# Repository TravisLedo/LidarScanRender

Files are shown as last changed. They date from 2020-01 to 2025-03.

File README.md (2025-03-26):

# Lidar Scan & Render Bot

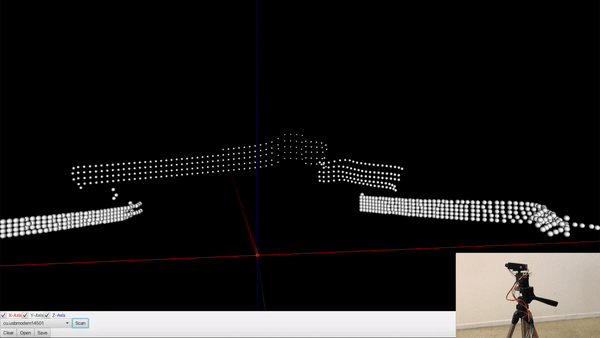
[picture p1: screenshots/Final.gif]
Results


## Video Link

* [YouTube](https://youtu.be/6YTCKRSWroE) - Video Demo

## How It Works
This project consists of two parts. The Arduino side handles all the servo movements and gets measurement readings from the Lidar sensor. The Java side does the spherical to cartesian points conversion and renders them in 3D. They communicate with each other over the serial port. The user can move around the scene with game-like fps controls for a better experience.

## The Math
There are two servos in the project. One will be used as the Pan (Phi) angle and the other as the Tilt (Theta) angle. The reading we get from the Lidar sensor will become the Radius. Which means that device itself would be at point (0,0,0). Each data set sent from the Arduino to the Java program consists of these three numbers (radius, phi, theta) with leading zeroes for consistency.

From here we have to convert these Spherical points to Cartesian(x, y, z) so we can properly plot them in our Java program.

We can achieve these conversions using these formulas.

Note: If you look inside the Java code and notice that some of the values of x, y, and z are swapped, some times even set to negative, that's because the computer coordinate system is different as well. For example, in computer coordinates, the x goes horizontal not y. Y positive goes down, not up. Things like that. These modifications made to the formula were only to get Java to render the points in the correct place.

## Serial Communication
I started this project with an Arduino Uno but ran into problems with the serial port conflicting with the servos. They cannot work at the same time. When data was being sent back and forth, the servos would jitter constantly. From research I learned that this was a common problem using SoftwareSerial. I found some workarounds for this problem but they were such a hassle and didn't work for me. I decided to switch to an Arduino Mega and it solved the jittering problem. This is because the Mega has multiple serial ports.

The steps of communicating

-Java opens port and listens for data
-Arduino takes first measurement, moves the servos to the next position and wait for an "Okay" signal from Java
 Arduino sends the data to Java in this format 000,000,000
-Java waits for all the fragments of data to reach a certain amount that is enough to convert
-Java converts those numbers, plots the point, and send the Arduino a single char as the "Okay" signal
-Once the Arduino receives the signal, it repeats what it did before at the new angle positions

The reason Java has to wait is because even though you tell the Arduino to send 9 digits and 2 commas, sending data over serial does not work that way. It will send fragments of whatever data it wants whenever it can. So we want Java to until all the data received looks like something it can recognize.

I used a USB cable as the serial connection but I am sure one could use a bluetooth module as well if wireless was needed.

## Powering The Project
I used a 5v wall brick to run the servos because I just hate dealing with batteries and avoid them when possible. The Lidar sensor was powered through the Arduino 5V. And of course the Arduino was powered with the same USB cable that was used as a serial port.

### Materials
* [Arduino Mega 2560](https://amzn.to/4c5rFt3)
* [Lidar Sensor](https://amzn.to/3XwOXC2)
* [Servo Motors](https://amzn.to/42jcc5k)
* [Brackets](https://amzn.to/3FSMJGZ)

### Prerequisites

* [Java](https://www.java.com) - Java Runtime Environment
* [Arduino](https://www.arduino.cc/) - Arduino Mega Microcontroller
* [TFMini(UART)](https://www.sparkfun.com/products/14588) - TFMini Lidar sensor

* [MG996R Servo x 2](https://www.towerpro.com.tw/product/mg996r/) - 180 degrees standard servos

## Programmed In

* [IntelliJ](https://www.jetbrains.com/idea/download) - Java IDE
* [Arduino](https://https://www.arduino.cc/) - Arduino IDE

## Schematic

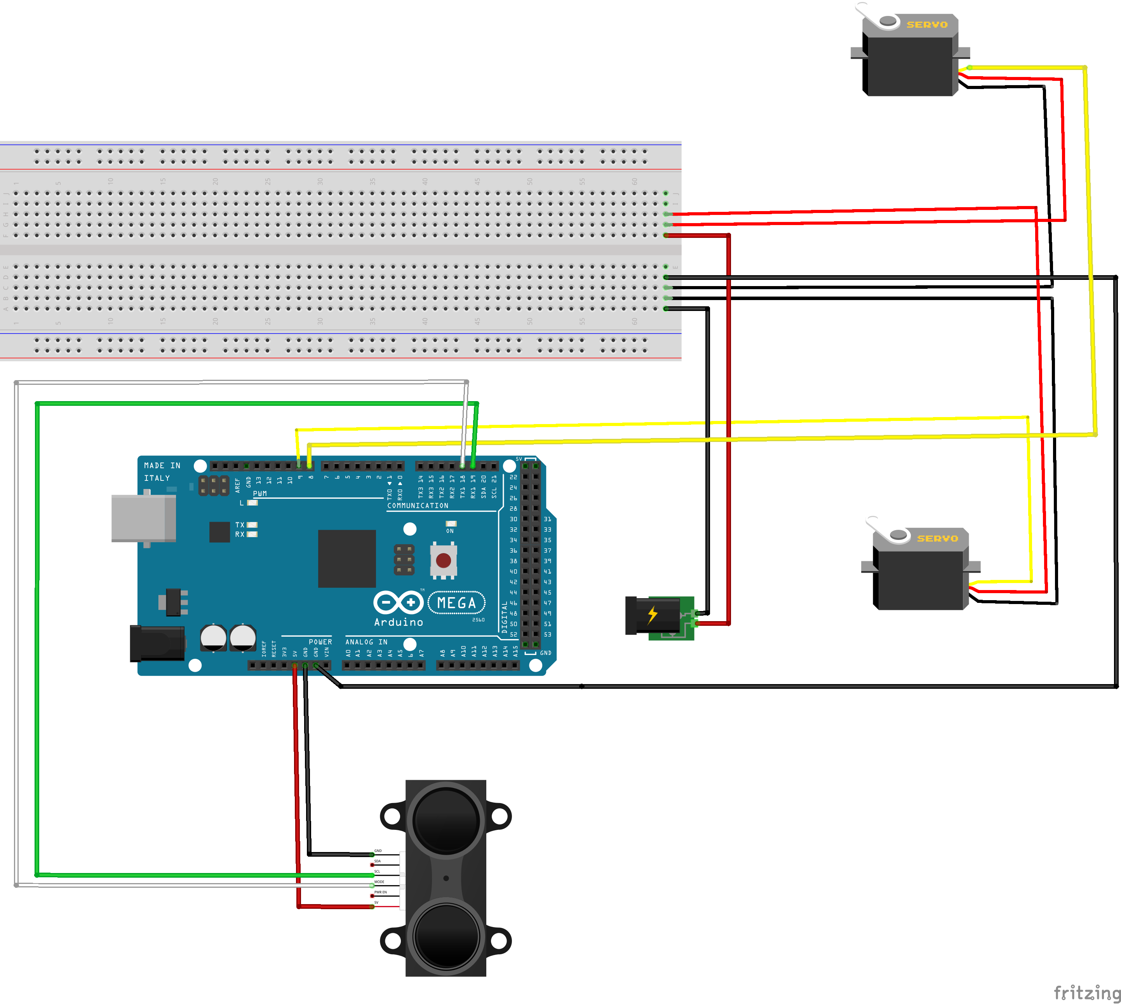
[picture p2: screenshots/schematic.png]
Schematic


## Screenshots

The Device
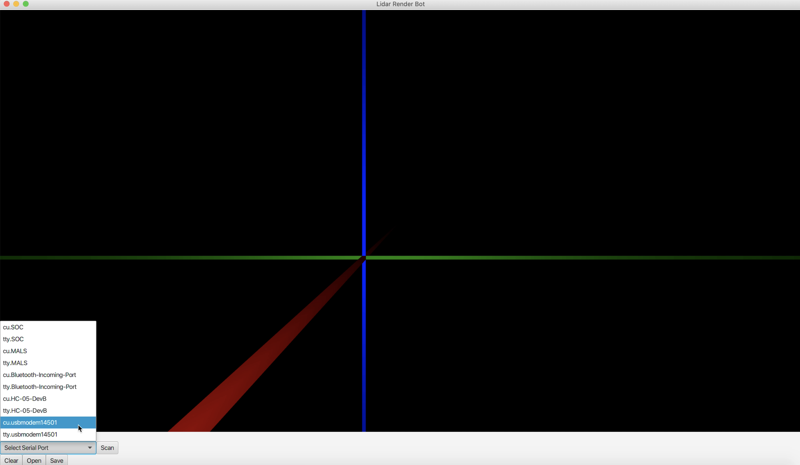
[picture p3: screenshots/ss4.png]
The Software

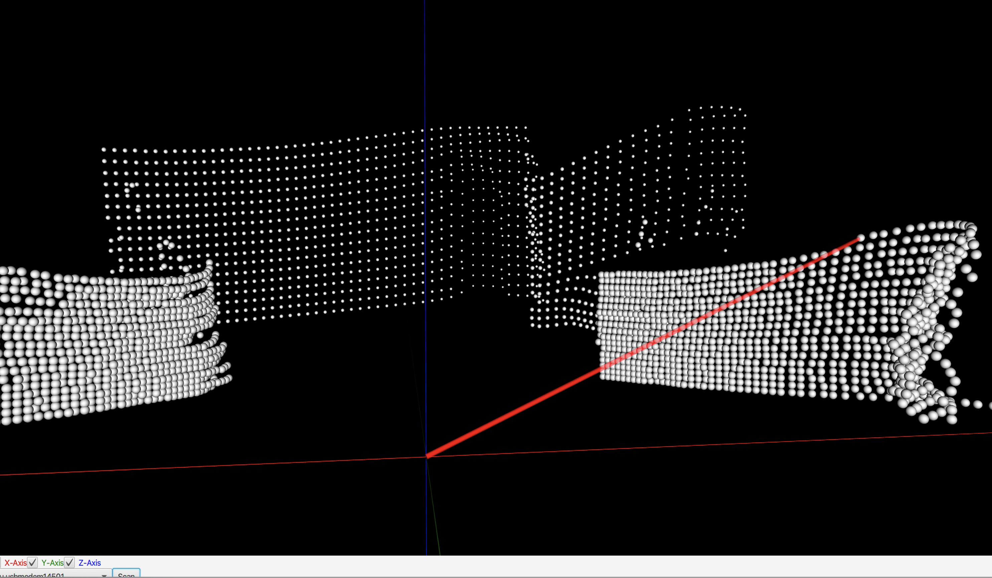
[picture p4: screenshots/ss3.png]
Running The Program

Results

## Authors

* **[Travis Ledo](https://travisledo.github.io)** - *Initial work* - [LidarScanRender](https://github.com/TravisLedo)

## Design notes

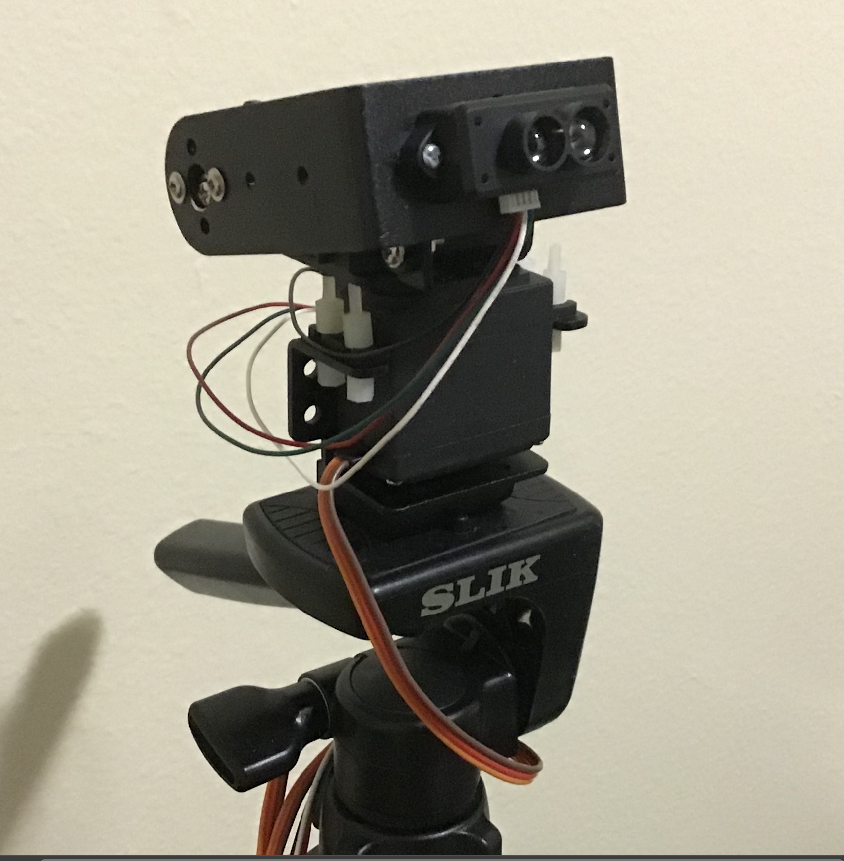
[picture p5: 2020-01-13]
screenshots/ss1.png

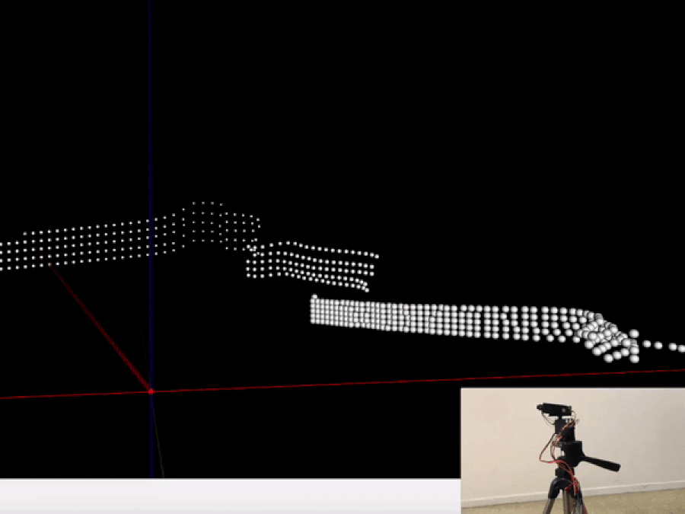
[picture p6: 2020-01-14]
screenshots/FinalCroppedGif.gif

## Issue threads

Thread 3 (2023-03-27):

Data not outputting correctly

tpats98, 2023-03-27:
Hi Travis,

I am a graduate student working on a project to eventually be able to scan and map underwater interiors such as caves and wrecks. I found your project and have been attempting to replicate it in my own way. I'm using Arduino to control my servo/LiDAR system as well as perform the conversion calculations. The sensor I am using is a Garmin LiDAR Lite v3HP. I use Putty to put the data into an Excel file and I am then using a Matlab code to put that data into a point cloud format. So, it is not happening live as in your scan. I am running into issues where the point cloud that is created looks nothing like the room I scanned. One of the issues is I am not getting any straight edges as if it was scanning a wall. It seems as though it is giving me a circle just based on the cloud I am seeing. The point clouds just do not make sense compared to what it should be scanning. I attempted to attach a screenshot, I am not sure if it is visible. Overall, it seems that my inputs are good. I am getting my pan and tilt servo positions as well as a distance reading from my sensor. This makes me think the issue is somewhere in my calculations and post-processing or maybe it could be an issue with my sensor/setup itself.

I am new to Github so I wasn't sure how to reach you. My apologies if this isn't the appropriate way to contact you. I was hoping you might be willing to provide some aid to me as I try to solve my issues. I look forward to hearing from you!

Thank you,
Tim Patschorke

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

TravisLedo, 2023-03-27:
Hey Tim,

Thanks for taking interest in this project and your app is looking really good.

When making your points render on screen, did you account for all the conversions? You have to convert from spherical coordinates, to rectangular coordinates, and then also to computer screen coordinates as well. Screens have minor differences like the Y axis going down for positive, not up. I would start a simple scan with just a few points first where you kind of know what the results should be and then play around with the conversions until it looks right. Even better if you test with just only one servo at a time to eliminate one axis from the conversions.

Another thing to make sure is that you are not using an Arduino UNO, the MEGA is a better choice. This project requires more than one serial line. One for sending data to pc and also another for getting data from the lidar sensor to the Arduino.  They interfere with each other if there is only one and the software serial libraries also will not work.

I am sure you have done this but have u also tried just testing the sensor itself? Just moving your hand back and forth to make sure the distance output looks correct.

Hope one of these could help you solve the problem. Let me know how it goes. Good luck!

tpats98, 2023-03-27:
Hi Travis,

Thank you for the timely response. I am mostly accounting for the conversions. I am having my Arduino code perform the spherical to cartesian as it scans. I have done a little bit of tinkering with the conversion for the computer coordinate system but not as much.

I tried taking out an axis, as you mention, by only using the pan servo. I played around with this and different things over the weekend and the only thing that would make my cloud look remotely close was by creating my own range for x. Instead of using the data, I just created a 0-180 range that the distance value could be plotted against. This gave me a somewhat accurate depiction of what was in front of the sensor but it is not a true representation of the room obviously.

As for the board, I am using a Mega. I haven't run into any issue whatsoever in the actual operation of the servos and sensor so that is a plus haha.

As for the sensor, you are correct, I have tested it by itself. I did not see any problems jumping out at me.

Overall, do you think my issue is just in the conversions possibly? I guess my main confusion is why it is outputting as a half circle instead of straight lines as if it was scanning a wall or came to a corner. Any ideas on that other than conversion issues maybe?

TravisLedo, 2023-03-27:
Yea I am leaning towards a conversion issue, especially when it looks more spherical when plotted. I would try to send manual data from the Arduino into the app as well to see if you get what you expect on the screen. Start with with something simple like (0,0,0, (10,10,10) and see if the two points are plotting correctly then add more points to the test.  If this looks good then most likely a conversion issue.

Have you tried dramatically slowing down the servos' delay between each point to give it more time to move to position, scan, move to the next position? Did you scan one point multiple times and play around with using the average or median? Try to get random readings and see how consistent the scanner is at one position.

Also have you tried a different wall? lol. I know that lidar sucks on glossy surfaces as well as sharp corners.

tpats98, 2023-03-29:
Hey Travis,

I wanted to reach out again as  I have good news! I spent the last 2 days messing around with the conversions and it is looking like I am getting the scan I need. I have attached one in case you're interested. I just wanted to thank you again for pointing me in the right direction!
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

TravisLedo, 2023-03-29:
That is awesome to hear! Glad you got it resolved. Hope everything goes well with your underwater scanner project, it's looking really cool.

Closed 2023-03-29.

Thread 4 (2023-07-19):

Errors occuring when run

24harter, 2023-07-19:
Here is the error message that I have every time I set it to run, however no error appears when I hit build/build and clean.
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

TravisLedo, 2023-07-19:
>

Hey there, it looks like you are missing JavaFX library. That library is pretty confusing and is constantly changing. I would make sure you install that library first, specifically for your IDE.

24harter, 2023-07-19:
This is the library I have installed with the jar files in it:
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
With this I get the error above. Am I missing something or a different kind of error, I'm new to java so sorry if this seems like a stupid question.
Also, thanks for responding to my issue quickly, I really appreciate it.

TravisLedo, 2023-07-19:
> This is the library I have installed with the jar files in it: 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 The IDE is the latest installment of Netbeans With this I get the error above. Am I missing something or a different kind of error, I'm new to java so sorry if this seems like a stupid question. Also, thanks for responding to my issue quickly, I really appreciate it.

Hey no worries. I just updated the project to use Gradle. This will auto download all the libraries you need. I also changed to using IntelliJ so please download that and run instead of Netbeans. Let me know how it goes.

24harter, 2023-07-20:
I've switched over to IntelliJ and transferred all the files, however I'm currently stuck on trying to run it since figure out what configuration I need.

TravisLedo, 2023-07-20:
> I've switched over to IntelliJ and transferred all the files, however I'm currently stuck on trying to run it since figure out what configuration I need.

Make sure you delete all the files you had and just download the whole project again. Then open the project folder from IntelliJ (Not the main LidarScanRender folder but the sub one inside). Once it finish loading, right click on the App file and select Run. Tell me what errors you get.

24harter, 2023-07-20:
I have successfully ran the app, but when I connect it to the com port and hit scan, it doesn't seem to be working. The arduino has the code on it, but seems inactive when I click scan. None of the servos are moving and nothing is appearing on the app or intellij.

24harter, 2023-07-20:
I have checked my lidar sensor and servos and both were fine. I believe the issue is that my lidar sensor is a tf luna instead of a tf mini-s, as it was mislabelled

TravisLedo, 2023-07-20:
> I have checked my lidar sensor and servos and both were fine. I believe the issue is that my lidar sensor is a tf luna instead of a tf mini-s, as it was mislabelled

Ah gotcha. Just need to refactor the Arduino code to use your specific sensor's library instead of the one I am using. It should still work, but that will be beyond what I can help you with since I don't own that sensor (I don't even have the one I used on this project anymore either).. Maybe play around with the current sensor you have and see if you can get it working. The fun part any project is making it work for your needs and learning along the way.

Closed 2024-04-03.

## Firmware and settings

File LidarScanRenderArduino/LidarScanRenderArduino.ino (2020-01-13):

/*
   Program: Lidar Render Bot
   By: Travis Ledo
   Date: Jan 12th 2020
   Notes: This uses an Arduino Mega with multiple serial ports to avoid the SoftwareSerial and Servo conflicts.
*/




#include <Servo.h>
#include "CustomTFMini.h" //Needed to modify somecode in the original TFMini library

Servo tiltServo;
Servo panServo;

TFMini tfmini;

String incomingByte; // for incoming serial data

int minPanPos = 0;
int maxPanPos = 180;
int minTiltPos = 0;
int maxTiltPos = 90;

int panPos = minPanPos;    // variable to store the servo position
int tiltPos = minTiltPos;    // variable to store the servo position


bool keepScanning = true;
bool panForward = true;


void printPoint(int pan, int tilt, int dis) { //Java software will read these printed texts

  Serial.print(addLeadingZeros(pan));
  Serial.print(pan);
  Serial.print(",");
  Serial.print(addLeadingZeros(tilt));
  Serial.print(tilt);
  Serial.print(",");
  Serial.print(addLeadingZeros(dis));
  Serial.print(dis);
  Serial.println();

}




String addLeadingZeros(int number) //Add leading zeros so every number sent will always be 3 digits long for consistency
{
  String leadingZeros = "";

  if (number < 10)
  {
    leadingZeros = "00";
  }
  else if (number >= 10 && number < 100)
  {
    leadingZeros = "0";
  }
  else
  {
    leadingZeros = "";

  }

  return leadingZeros;
}




void updatePos() //move servos to next position
{
  if (panPos == maxPanPos)
  {
    panPos = 0;
    tiltPos++;
    panServo.write(panPos);
    tiltServo.write(tiltPos);
    delay(1000);
    keepScanning = true;
  }
  else if (panPos < maxPanPos)
  {
    panPos ++;
    panServo.write(panPos);
    delay(15);

    keepScanning = true;
  }

  if (tiltPos > maxTiltPos)
  {
    keepScanning = false;
  }
}




void takeMeasurement(int panPos, int tiltPos) //get a reading from the TFMini
{

  uint16_t dist1 = tfmini.getDistance();

  while (dist1 < 0 || dist1 > 1500)
  {
    dist1 = tfmini.getDistance();
  }


  uint16_t dist2 = tfmini.getDistance();

  while (dist2 < 0 || dist2 > 1500)
  {
    dist2 = tfmini.getDistance();
  }

  uint16_t dist3 = tfmini.getDistance();

  while (dist3 < 0 || dist3 > 1500)
  {
    dist3 = tfmini.getDistance();
  }



  uint16_t dist = dist1 + dist2 + dist3;

  uint16_t distAv = dist / 3;



  // Display the measurement
  printPoint(panPos, tiltPos, distAv);
  updatePos();
}





void setup() {

  panServo.attach(8);  // attaches the servo on pin
  tiltServo.attach(9);  // attaches the servo on pin

  // Step 1: Initialize hardware serial port 
  Serial.begin(115200); //For usb/bt data?

  // Step 2: Initialize the data rate for TFMini
  Serial1.begin(TFMINI_BAUDRATE);

  // Step 3: Initialize the TF Mini sensor
  tfmini.begin(&Serial1);

  panServo.attach(8);  // attaches the servo on pin
  tiltServo.attach(9);  // attaches the servo on pin
  tiltServo.write(tiltPos);
  panServo.write(panPos);
  delay(2000);


  //start first measurement
  takeMeasurement(panPos, tiltPos);

}



void loop() {

  if (tiltPos > maxTiltPos) //end program succesfully
  {
    keepScanning = false;
  }

  // send data only when you receive data:
  if (Serial.available() > 0 && keepScanning) {
    keepScanning = false; //need this to make the loop not go so fast
    takeMeasurement(panPos, tiltPos);
  }
}

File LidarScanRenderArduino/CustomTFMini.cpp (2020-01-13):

/*
Arduino driver for Benewake TFMini time-of-flight distance sensor. 
by Peter Jansen (December 11/2017)
This code is open source software in the public domain.

THIS SOFTWARE IS PROVIDED ''AS IS'' AND ANY
EXPRESS OR IMPLIED WARRANTIES, INCLUDING, BUT NOT LIMITED TO, THE IMPLIED
WARRANTIES OF MERCHANTABILITY AND FITNESS FOR A PARTICULAR PURPOSE ARE
DISCLAIMED. IN NO EVENT SHALL THE AUTHOR(S) BE LIABLE FOR ANY
DIRECT, INDIRECT, INCIDENTAL, SPECIAL, EXEMPLARY, OR CONSEQUENTIAL DAMAGES
(INCLUDING, BUT NOT LIMITED TO, PROCUREMENT OF SUBSTITUTE GOODS OR SERVICES;
LOSS OF USE, DATA, OR PROFITS; OR BUSINESS INTERRUPTION) HOWEVER CAUSED AND
ON ANY THEORY OF LIABILITY, WHETHER IN CONTRACT, STRICT LIABILITY, OR TORT
(INCLUDING NEGLIGENCE OR OTHERWISE) ARISING IN ANY WAY OUT OF THE USE OF THIS
SOFTWARE, EVEN IF ADVISED OF THE POSSIBILITY OF SUCH DAMAGE.  

The names of the contributors may not be used to endorse or promote products
derived from this software without specific prior written permission.
*/

#include "CustomTFMini.h"

// Constructor
TFMini::TFMini() { 
  // Empty constructor
}


boolean TFMini::begin(Stream* _streamPtr) {
  // Store reference to stream/serial object
  streamPtr = _streamPtr;

  // Clear state
  distance = -1;
  strength = -1;
  state = READY;
  
  // Set standard output mode
  setStandardOutputMode();
  
  return true;
}


// Public: The main function to measure distance. 
uint16_t TFMini::getDistance() {
  int numMeasurementAttempts = 0;
  while (takeMeasurement() != 0) {
    numMeasurementAttempts += 1;
    if (numMeasurementAttempts > TFMINI_MAX_MEASUREMENT_ATTEMPTS) {
     // Serial.println ("TF Mini error: too many measurement attempts");
     // Serial.println ("Last error:");
    //  if (state == ERROR_SERIAL_NOHEADER)     Serial.println("ERROR_SERIAL_NOHEADER");
    //  if (state == ERROR_SERIAL_BADCHECKSUM)  Serial.println("ERROR_SERIAL_BADCHECKSUM");
    //  if (state == ERROR_SERIAL_TOOMANYTRIES) Serial.println("ERROR_SERIAL_TOOMANYTRIES");
      
      state = ERROR_SERIAL_TOOMANYTRIES;
      distance = -1;
      strength = -1;      
      return -1;      
    }
  }

  if (state == MEASUREMENT_OK) {
    return distance;
  } else {
    return -1;
  }
}

// Public: Return the most recent signal strength measuremenet from the TF Mini
uint16_t TFMini::getRecentSignalStrength() {
  return strength;
}


// Private: Set the TF Mini into the correct measurement mode
void TFMini::setStandardOutputMode() {
  // Set to "standard" output mode (this is found in the debug documents)
  streamPtr->write((uint8_t)0x42);
  streamPtr->write((uint8_t)0x57);
  streamPtr->write((uint8_t)0x02);
  streamPtr->write((uint8_t)0x00);
  streamPtr->write((uint8_t)0x00);
  streamPtr->write((uint8_t)0x00);
  streamPtr->write((uint8_t)0x01);
  streamPtr->write((uint8_t)0x06);
}

// Set configuration mode
void TFMini::setConfigMode() {
  // advanced parameter configuration mode
  streamPtr->write((uint8_t)0x42);
  streamPtr->write((uint8_t)0x57);
  streamPtr->write((uint8_t)0x02);
  streamPtr->write((uint8_t)0x00);
  streamPtr->write((uint8_t)0x00);
  streamPtr->write((uint8_t)0x00);
  streamPtr->write((uint8_t)0x01);
  streamPtr->write((uint8_t)0x02);  
}

// Set single scan mode (external trigger)
void TFMini::setSingleScanMode() {
  setConfigMode();
  // setting trigger source to external
  streamPtr->write((uint8_t)0x42);
  streamPtr->write((uint8_t)0x57);
  streamPtr->write((uint8_t)0x02);
  streamPtr->write((uint8_t)0x00);
  streamPtr->write((uint8_t)0x00);
  streamPtr->write((uint8_t)0x00);
  streamPtr->write((uint8_t)0x00);
  streamPtr->write((uint8_t)0x40);
}

// Send external trigger
void TFMini::externalTrigger() {
  setConfigMode();      
  // send trigger
  streamPtr->write((uint8_t)0x42);
  streamPtr->write((uint8_t)0x57);
  streamPtr->write((uint8_t)0x02);
  streamPtr->write((uint8_t)0x00);
  streamPtr->write((uint8_t)0x00);
  streamPtr->write((uint8_t)0x00);
  streamPtr->write((uint8_t)0x00);
  streamPtr->write((uint8_t)0x41);
}

// Private: Handles the low-level bits of communicating with the TFMini, and detecting some communication errors.
int TFMini::takeMeasurement() {
  int numCharsRead = 0;
  uint8_t lastChar = 0x00;  
  
  // Step 1: Read the serial stream until we see the beginning of the TF Mini header, or we timeout reading too many characters.
  while (1) {

    if (streamPtr->available()) {      
      uint8_t curChar = streamPtr->read();

      if ((lastChar == 0x59) && (curChar == 0x59)) {
        // Break to begin frame
        break;
        
      } else {
        // We have not seen two 0x59's in a row -- store the current character and continue reading.         
        lastChar = curChar;
        numCharsRead += 1; 
      }           
    }

    // Error detection:  If we read more than X characters without finding a frame header, then it's likely there is an issue with 
    // the Serial connection, and we should timeout and throw an error. 
    if (numCharsRead > TFMINI_MAXBYTESBEFOREHEADER) {
      state = ERROR_SERIAL_NOHEADER;
      distance = -1;
      strength = -1;     
     // if (TFMINI_DEBUGMODE == 1) Serial.println("ERROR: no header");
      return -1;      
    }
    
  }
  
  // Step 2: Read one frame from the TFMini
  uint8_t frame[TFMINI_FRAME_SIZE];

  uint8_t checksum = 0x59 + 0x59;
  for (int i=0; i<TFMINI_FRAME_SIZE; i++) {
    // Read one character
    while (!streamPtr->available()) {
      // wait for a character to become available
    }    
    frame[i] = streamPtr->read();

    // Store running checksum
    if (i < TFMINI_FRAME_SIZE-2) {
      checksum += frame[i];
    }
  }

  // Step 2A: Compare checksum
  // Last byte in the frame is an 8-bit checksum 
  uint8_t checksumByte = frame[TFMINI_FRAME_SIZE-1];
  if (checksum != checksumByte) {
    state = ERROR_SERIAL_BADCHECKSUM;
    distance = -1;
    strength = -1;
   // if (TFMINI_DEBUGMODE == 1) Serial.println("ERROR: bad checksum");
    return -1;
  }


  // Step 3: Interpret frame
  uint16_t dist = (frame[1] << 8) + frame[0];
  uint16_t st = (frame[3] << 8) + frame[2];
  uint8_t reserved = frame[4];
  uint8_t originalSignalQuality = frame[5];


  // Step 4: Store values
  distance = dist;
  strength = st;
  state = MEASUREMENT_OK;

  // Return success
  return 0;  
}

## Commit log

2020-01-13 Added Screenshots
    [LidarScanRender.fzz]
2020-01-20 Add Screenshot
    [LidarScanRender.fzz]
